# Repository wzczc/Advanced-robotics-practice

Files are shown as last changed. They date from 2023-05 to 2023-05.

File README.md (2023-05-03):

# Advanced-robotics-practice
code for "机器人高级实践"，**双轮足平衡小车**，实现细节见.docx文件  
小车整体图

* 小车硬件：**hardware** 文件夹
* 小车建模：**solidworks_models** 文件夹，小车轮腿图：
小车轮腿建模

* 开发平台：**STM32CubeMX** 和 **keil5** 联合开发
* 小车运行工程：**code-->MDK-ARM-->Encoder.uvprojx**
* 功能：
  * **平衡与抗干扰**

https://user-images.githubusercontent.com/94534877/235918275-014c7818-3400-4d11-a03c-7880798e8d1c.mp4

  * **轮腿伸缩**

https://user-images.githubusercontent.com/94534877/235918329-b2903bcf-4b72-4534-91ec-1fd617b79910.mp4

  * **直立行走**：可以使用手机蓝牙app(code文件夹里的base.apk.1)控制小车的前进、后退、左转、右转和停止

https://user-images.githubusercontent.com/94534877/235919043-f2ff14f8-f3b6-48d8-b337-52a1ab3aed3c.mp4

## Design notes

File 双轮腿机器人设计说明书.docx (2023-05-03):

1、 机器人总体介绍

1、设计原因

本款机器人名为双轮腿机器人，顾名思义，是以左右轮来代替传统的足式机器人的双脚，同时保留其腿式结构，使其既能像轮式机器人一样迅速，又能像足式机器人一样适应复杂的地形，从而满足我们对不同场景的各种各样的需求。

2、设计思路

本款机器人以腾讯近期发布的Ollie为基础，结合哔哩哔哩国炫学长的开源资料，自主设计机器人的机械结构与硬件选型；其中设计软件采用SolidWorks，采用3D打印的方式打印机器人的本体；硬件选择了四个舵机来控制机器人的四条大腿，大腿和小腿之间用轴承连接成旋转关节，小腿分别嵌在左右电机上，如此可以通过舵机来控制机器人的升降；电机采用带编码器的直流电机，信息实时传入主控板是stm32中，结合MPU6050测量的角度信息，从而控制车的基本平衡以及行走平衡。

3、基本功能

本款机器人目前实现的功能主要有：

1)能够实现基本的直立平衡状态；

2)给予人为干扰能保持平衡状态；

3)能够完成移动动作而保持不倒；

4)能够在移动时改变自己的移动方向；

5)能够在直立时完成腿部的升、降；

后续功能敬请期待！

4、优点
1)结构简单、双驱动，转角大且转弯半径小，甚至能实现原地回转，这使得两轮机器人运动十分灵活，线路轨迹多变，能够在空间狭窄的地区进行作业，克服了多轮机器人空间受限的缺点;

2)占地面积也小，由于机体一般采用分层设计，合理利用了空间，适用场所大大增加，作为短距离代步工具和娱乐机器人等都十分方便，也为机器人的小型化发展提供了参考方案;
3)低碳环保,所需驱动功率小，使用蓄电池供电就可满足电机运动需求，而且直驱电机噪音小、动力强劲，对节能有一定的积极作用;
4)能量损耗少，由于车轮数量只有两个，地面摩擦引起的损耗减少，并且两轮自平衡机器人没有刹车系统，不存在刹车片磨损等问题，制动仅靠控制器发出的电机运动指令，由电机转矩控制整个机器人运动或停止，这有利于提高物理能量利用率。

二、机器人本体介绍

机器人本体结构是机体结构和机械传动系统 (https://baike.baidu.com/item/%E6%9C%BA%E6%A2%B0%E4%BC%A0%E5%8A%A8%E7%B3%BB%E7%BB%9F/14743222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)，也是机器人的支承基础和执行机构。机器人本体基本结构由以下五部分组成：传动部件、机身及行走机构、臂部、腕部、手部。

本款机器人目前只包含机器人本体的两部分，即传动部件和机身及行走机构。 传动部件：主要是双轮腿机器人的四条腿与其相连接的部分构成多个旋转关节。舵机的旋转带动大腿的旋转；大腿通过轴承带动小腿的旋转；机器人腿部形状由张开到蜷缩在一起；高度下降，重心降低；舵机反方向旋转，机器人腿部打开，高度升高，重心升高。

机身及行走结构：机身框架由顶部的双层支撑板通过舵机与大腿相连，大腿连接小腿，小腿通过轴承连接电机，电机嵌在法兰上，外部连接车轮。其中支撑板用来固定主控板stm32、舵机、MPU6050、电机驱动模块、降压稳压模块和电源。行走结构即电机卡在法兰上连接车轮从而驱动电机使车轮转动，达到行走动作。

后续可以在双轮腿机器人的顶部支撑板安装机械臂，从而弥补其他三个结构的空缺，使机器人能够满足更多的需求。

三、硬件部分

硬件部分包括：24v电池一块，降压模块，驱动模块，MG996R舵机*4，有刷电机*2，核心板STM32F407,陀螺仪MPU6050*1.

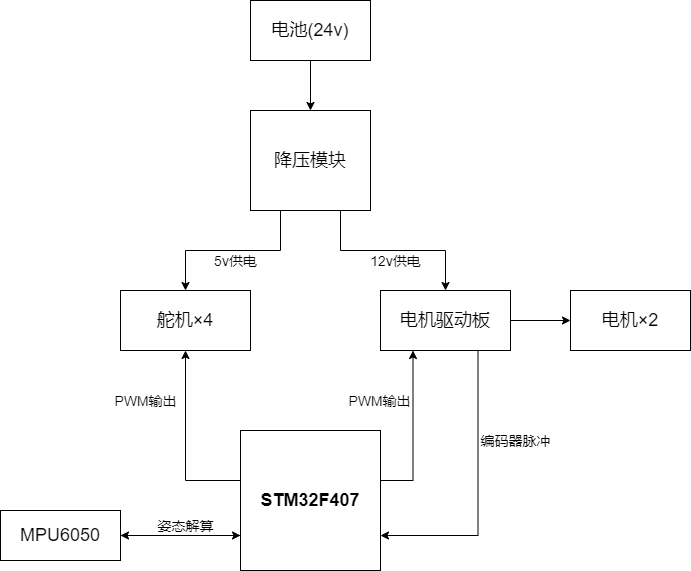
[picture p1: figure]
硬件框图

1.电池（24V）

2.降压型DC-DC电源模块XL4005

输入DC电压5-32V，输出DC电压0.8-30V，可实现双通道输出，输出电压比输入电压要低，只能通过模块内的精密电位器达到降压而不能升压。输出电流最大为5A，转换效率为92%。

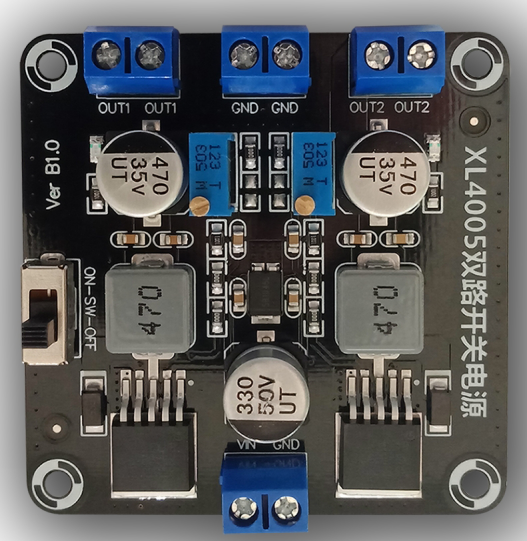
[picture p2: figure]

3.电机驱动模块AT8236

AT8236 芯片是一款单通道H桥电机驱动器，能够以高达6A的峰值电流双向控制单个电机。此模块内置两个AT8236，因此一个模块可以控制两个电机运转。芯片内部集成同步整流功能，能够有效降低系统功耗要求。利用电流衰减模式，可通过对输入信号进行脉宽调制(PWM) 来控制电机转速。此外，芯片对外还提供一个参考电压（Vref）输入引脚，用来设定驱动峰值电流的大小，此5V带稳压模块内的Vref引脚输入电压为5V。

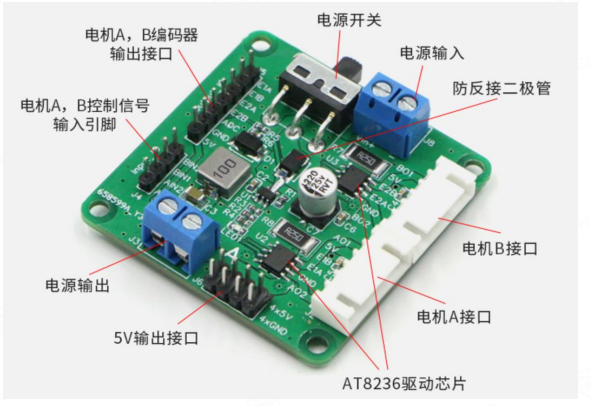
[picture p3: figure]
QQ截图20230224171222

4.MG996R舵机

和普通舵机一样，是一种位置伺服的驱动器，适用于那些需要角度不断变化并且可以保持的控制系统。其工作原理是：控制信号由接收机的通道进入信号调制芯片，获得直流偏置电压。它内部有一个基准电路，产生周期为20ms,宽度为1.5ms的基准信号，将获得的直流偏置电压和电位器的电压比较，获得电压输出。最后，电压差的正负输出到电机驱动芯片决定电机的正反转，当电机转速一定时，通过级联减速齿轮带动电位器旋转，使得电压差为0，电机停止转动。舵机的控制信号是PWM信号，利用占空比的变化改变舵机的位置。

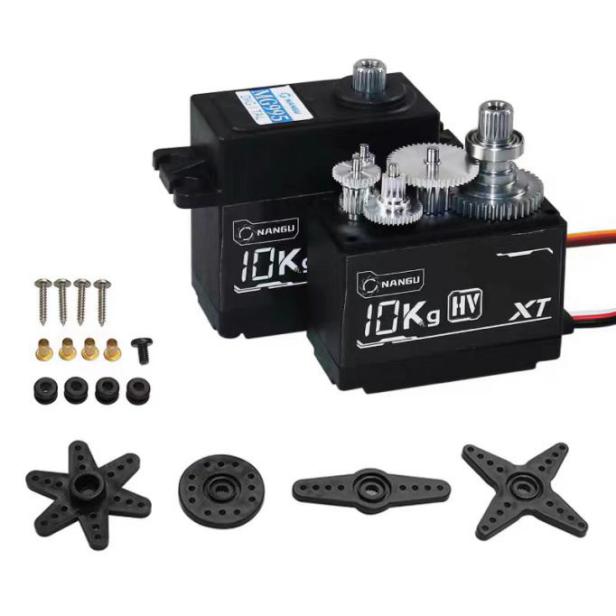
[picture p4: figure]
tb_image_share_1677231199930

5.带霍尔编码器的电机MG513P60

减速电机是在直流电机基础上，增加一个高精密的减速器的电机。一般直流电机的转速在一分钟几千上万转，增加减速器可以降低电机转速，增加电机扭矩，使得可控性更强。

选择减速电机的时候，电机的额定电压需要和我们选择的电池相匹配，常见的12V额定电压电机供电范围在11~16V之间，12V最佳。MG513P60_12V这款电机额定电压为12V，1：60的减速比，额定输出电流为0.36A，减速后空载转速为183rpm左右，扭矩达2kg*cm，最大负载能力高达6KG，再搭配65mm直径轮胎，速度大概0.5m/s，完全满足平衡小车的运动需求。另外这款电机还搭配了霍尔编码器，通过磁感应的原理，可以检测电机转速，从而实现速度检测和距离统计。

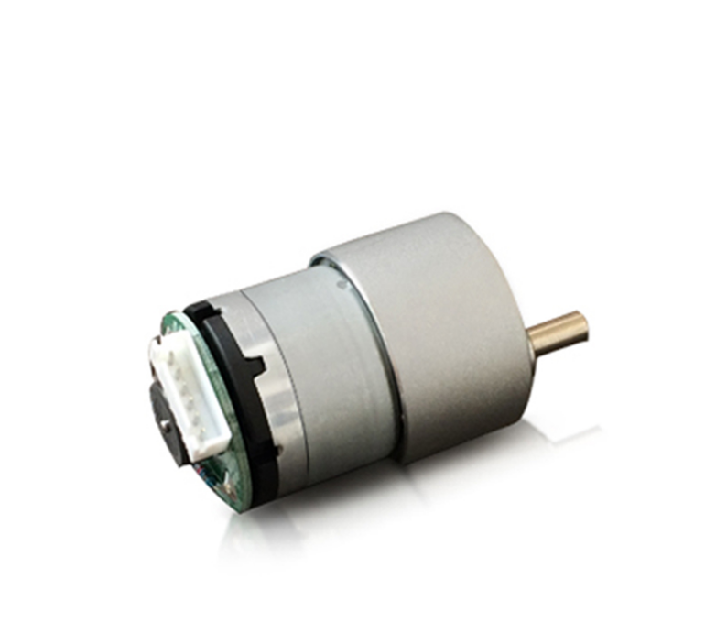
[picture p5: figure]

6.主控板STM32F407

STM32F407系列面向需要在小至10 x 10 mm的封装内实现高集成度、高性能、嵌入式存储器和外设的医疗、工业与消费类应用。
STM32F407/417提供了工作频率为168 MHz的Cortex™-M4内核（具有浮点单元）的性能。

性能：在168 MHz频率下，从Flash存储器执行时，STM32F407能够提供210 DMIPS/566 CoreMark性能，并且利用意法半导体的ART加速器实现了FLASH零等待状态。DSP指令和浮点单元扩大了产品的应用范围。

功效：该系列产品采用意法半导体90 nm工艺和ART加速器，具有动态功耗调整功能，能够在运行模式下和从Flash存储器执行时实现低至238 µA/MHz的电流消耗（@ 168 MHz）。

丰富的连接功能：出色的创新型外设：与STM32F4x5系列相比，STM32F407产品还具有符合IEEE 1588 v2标准要求的以太网MAC10和能够连接CMOS照相机传感器的8~14位并行照相机接口。

·2个USB OTG（其中一个支持HS）

·音频：专用音频PLL和2个全双工I²S

·通信接口多达15个（包括6个速度高达11.25 Mb/s的USART、3个速度高达45 Mb/s的SPI、3个I²C、2个CAN和1个SDIO）

·模拟：2个12位DAC、3个速度为2.4 MSPS或7.2 MSPS（交错模式）的12位ADC

·定时器多达17个：频率高达168 MHz的16和32位定时器

·可以利用支持Compact Flash、SRAM、PSRAM、NOR和NAND存储器的灵活静态存储器控制器轻松扩展存储容量

·基于模拟电子技术的真随机数发生器

STM32F407产品系列具有512KB~1MB Flash和192KB SRAM，采用尺寸小至10 x 10 mm的100~176引脚封装。

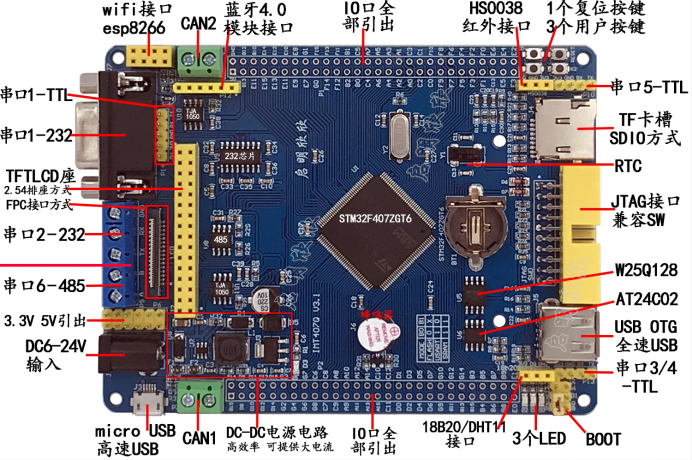
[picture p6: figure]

7.MPU6050

MPU-6050 是6轴运动处理传感器，它集成了 3 轴MEMS陀螺仪，3 轴MEMS加速度计，以及一个可扩展的数字运动处理器DMP。使用它就是为了得到待测物体（如四轴飞行器、平衡小车）x、y、z轴的倾角（俯仰角Pitch、翻滚角Roll、偏航角Yaw）。我们通过 I2C 读取到 MPU6050 的六个数据（三轴加速度 AD 值、三轴角速度 AD 值）经过姿态融合后就可以得到 Pitch、Roll、Yaw角。机器人搭载MPU-6050后测出实时三轴加速度和三轴角速度值，返回的数据反映小车姿态，相关程序处理后控制小车平衡。

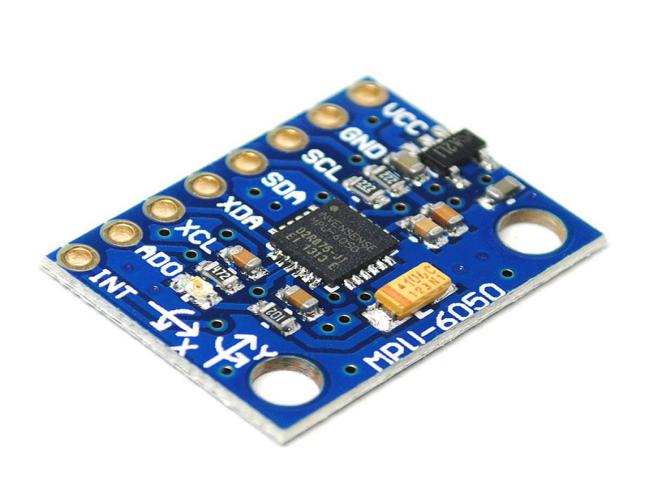
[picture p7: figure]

最后搭建出来的实物为：

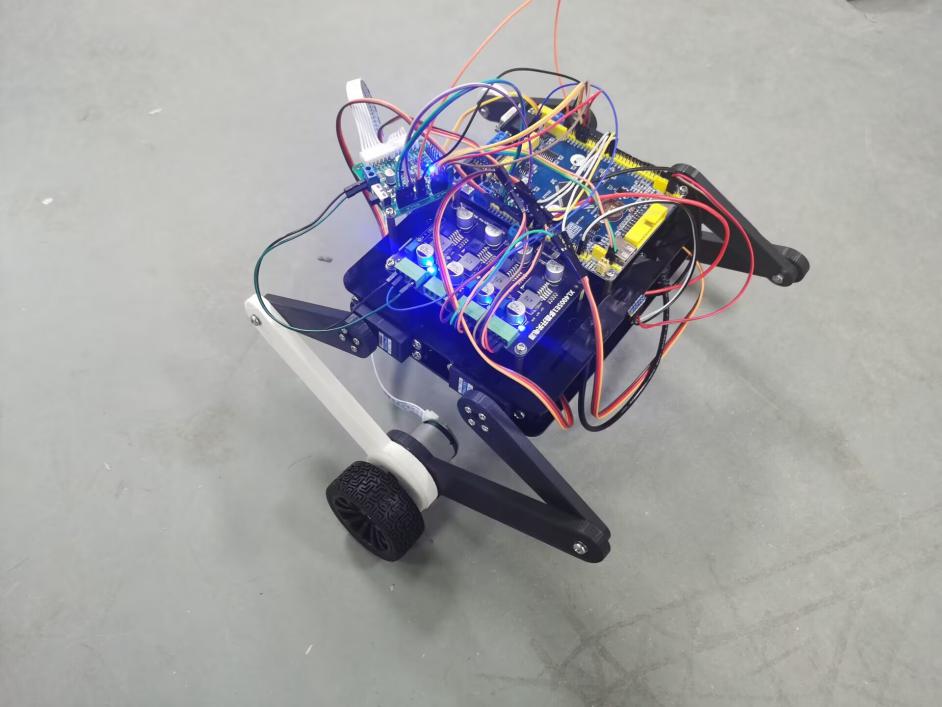
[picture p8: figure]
7E81C18BE3AB505F0FD8E452D66519CA

4、 软件

1.开发工具

使用keil 5和STM32CubeMX联合编写代码。keil5是一款单片机的软件开发系统，功能十分强大；

STM32CubeMX是STM32芯片的图形化操作界面，可以以图形界面的方式很方便地给所需功能进行配置，并且自动生成HAL库的配置代码，免去了自己查手册编写配置代码的繁琐步骤。

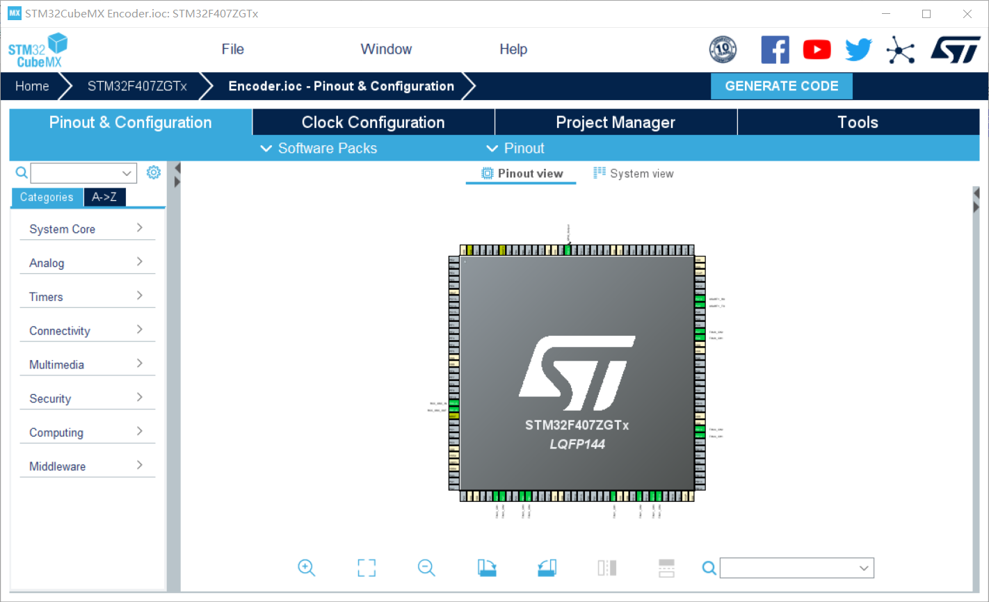
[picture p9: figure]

2.软件资源

GPIO：

1)PG13：作GPIO输出功能，用来点亮LED灯从而判断达到了某些状态。我们这里用它的闪烁来指示进入了定时器中断；

2)PF6、7、8、9：上拉输入模式，用来判断按键是否按下从而切换不同的模式。

TIM定时器：

1)TIM1：四个通道均作PWM生成功能，对应的引脚为PE9、PE11、PE13、PE14，使用如下函数：

控制TIM1不同的通道生成不同占空比的PWM波从而驱动电机。

2)TIM2：作计时功能。TIM2定时器的时钟频率是84MHz，我们设置预分频系数为840，自动重装载值为500：

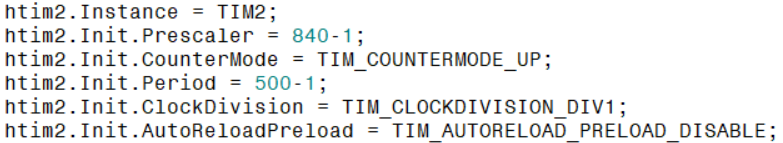
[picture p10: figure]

因此就可产生5ms的定时器中断，并在中断函数中编写控制算法控制小车的平衡。

3)TIM3：与TIM1一样，四个通道均作PWM生成功能，对应的引脚为PA6、PA7、PB0、PB1，产生不同占空比的PWM波控制舵机旋转的角度。

4)TIM4、8：使用它们的编码器模式功能，对应引脚为PD12、PD13、PC6、PC7，调用如下函数：

可获得左右两个轮子的编码器读数。

USART1：发送数据的功能，用到的引脚PA9、PA10。在这里，我们这里配合无线下载器传输平衡车的状态数据（车的速度和yaw、pitch、roll三个角度）发到电脑上的串口调试助手，以实时观察小车的状态。

DMP：MPU6050的加速库，用来加速MPU6050的数据处理。

蓝牙模块上位机：使用蓝牙app在手机上控制小车的前进、后退、左转、右转和停止：

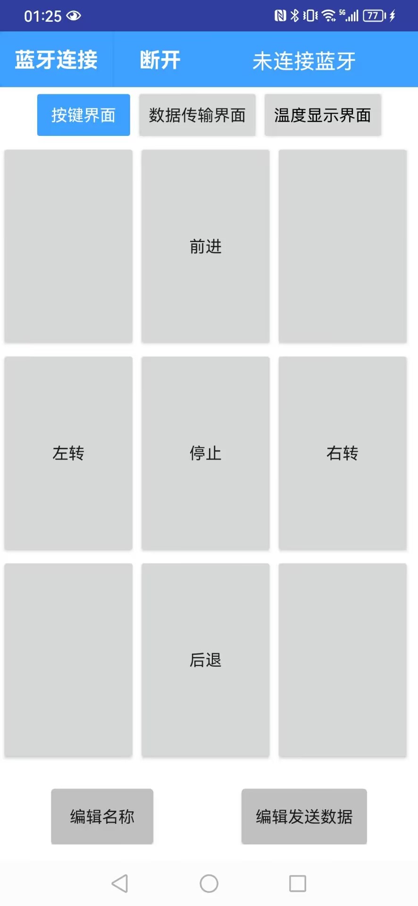
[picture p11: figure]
33618EE7FDCFAD0122F62B28D3B00625

相关的通信协议如下：

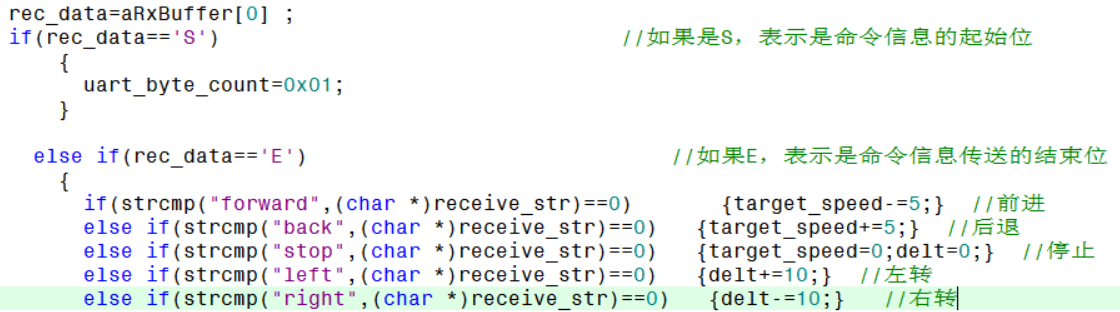
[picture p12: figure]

3.控制算法

使用的是两环并级PID算法，分别是PD调节的直立环（正反馈）和PI调节的速度环（负反馈），程序设计流程如下：

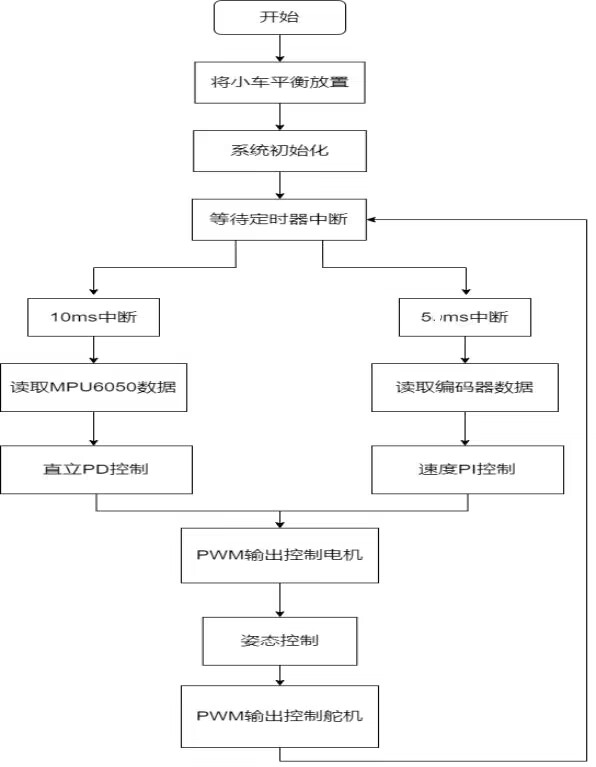
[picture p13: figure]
AC344A784FE81C7BA1DF45E036AFA032

五、操作流程

我们分别给小车设置了按键控制模式和蓝牙控制模式

1.按键控制模式

使用单片机上的四个按键来对应四个不同的模式：

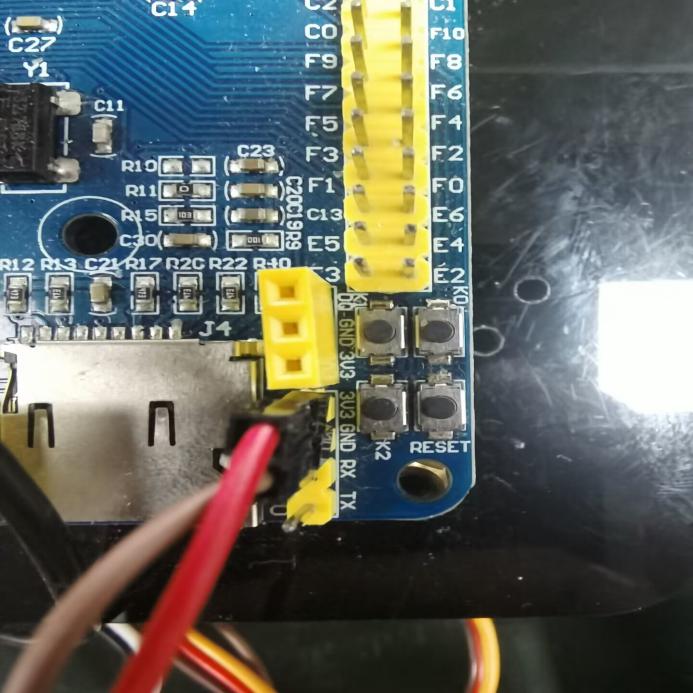
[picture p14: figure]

KEY0（右下按键）：为启动小车和平衡模式的按键。首先将小车放在大致的平衡位置，按下KEY0，小车可以在舵机转角为10°的情况下保持稳定平衡，之后轻拍小车，小车会有短暂的摇晃但马上可以恢复平衡状态。此模式展示的是小车平衡状态以及其抗干扰的性能。

KEY1（右上按键）：为平衡状态下伸缩腿模式的按键。首先将小车放在大致的平衡位置，按下KEY1，小车在短暂平衡后舵机转角会从10°连续改变至35°，在35°下短暂平衡后，舵机转角又会恢复至10°，如此反复。此模式展示的是小车在腿上下伸缩的情况下仍能保持平衡的性能。

KEY2（左上按键）：为小车行驶模式的按键。首先将小车放在大致的平衡位置，按下KEY2，在短暂平衡后，小车会开始逐渐向前加速至设定值，行驶一段时间后停止并平衡，之后在向后行驶一段时间再平衡。此模式展示的是小车可以稳定平衡行驶的性能。

KEY3（左下按键）：为小车行驶状态下伸缩腿模式的按键。首先将小车放在大致的平衡位置，按下KEY3，在短暂平衡后，小车会开始向前行驶，并在行驶过程中将腿抬起至25°随后再降至10°，如此反复。此模式展示的是小车在行驶时腿可以反复上下屈伸的性能。

2. 蓝牙控制模式

首先将小车放置在大致平衡位置，启动小车；然后打开蓝牙app与小车上的蓝牙模块HC-05配对；之后在app里设置发送给小车的数据以控制小车不同的运动，我们这里设置了如下5个运动方式：

按下相应的键，小车就会有不同的运动，并且按键次数的不同也会有不同的速度，如按一次“前进”是缓慢前进，连续按两三次“前进”则是快速前进，其他按键的运动模式亦是如此。

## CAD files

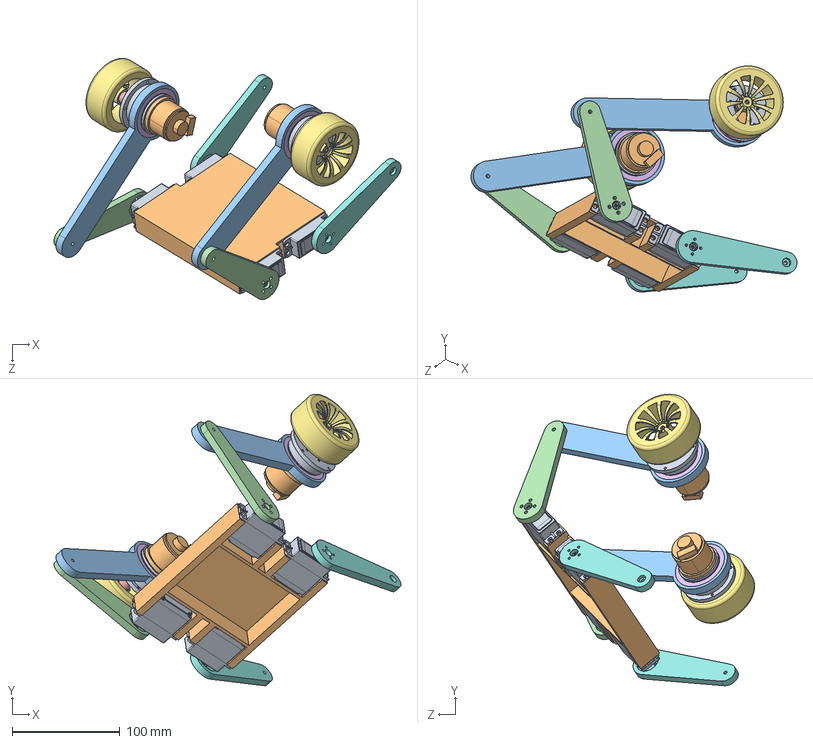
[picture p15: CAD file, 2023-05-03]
solidworks_models/轮腿.SLDASM
322.0 x 270.5 x 223.7 mm
打印件 x 2
马达三维模型 x 2
small leg2 x 2
大腿 x 2
轴直径6mm_车轮65mm联轴器.stp x 2
零件4 x 2
智能车轮_直径65mm.stp x 2
大腿 2 x 2
标准舵机外形3D.step x 4
车头

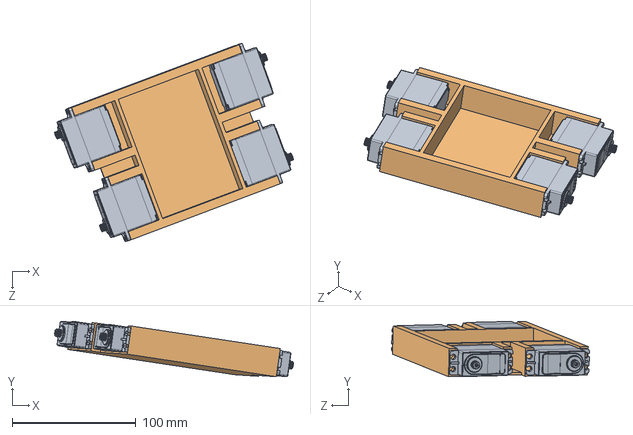
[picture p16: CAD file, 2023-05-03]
solidworks_models/盒.SLDASM
193.3 x 44.8 x 160.1 mm
标准舵机外形3D.step x 4
车头

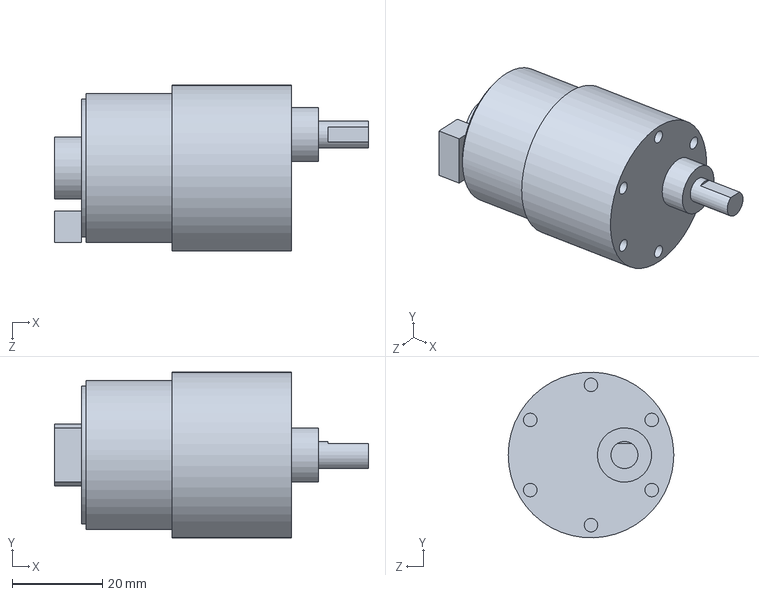
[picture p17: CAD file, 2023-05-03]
solidworks_models/马达.SLDPRT
69.4 x 36.6 x 36.6 mm

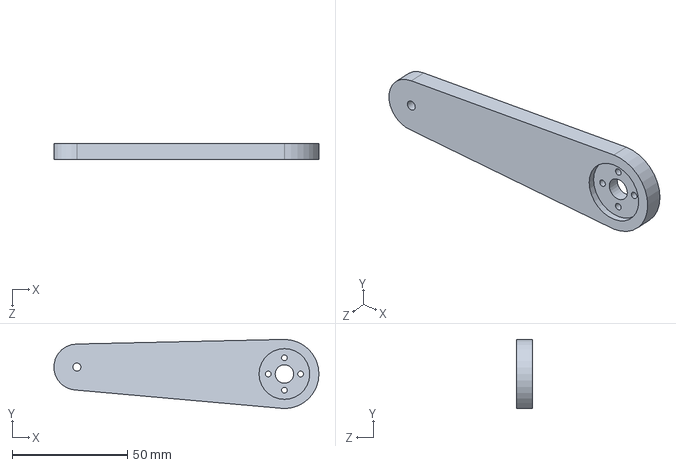
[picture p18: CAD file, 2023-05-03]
solidworks_models/大腿 2.SLDPRT
114.9 x 30.0 x 7.00 mm

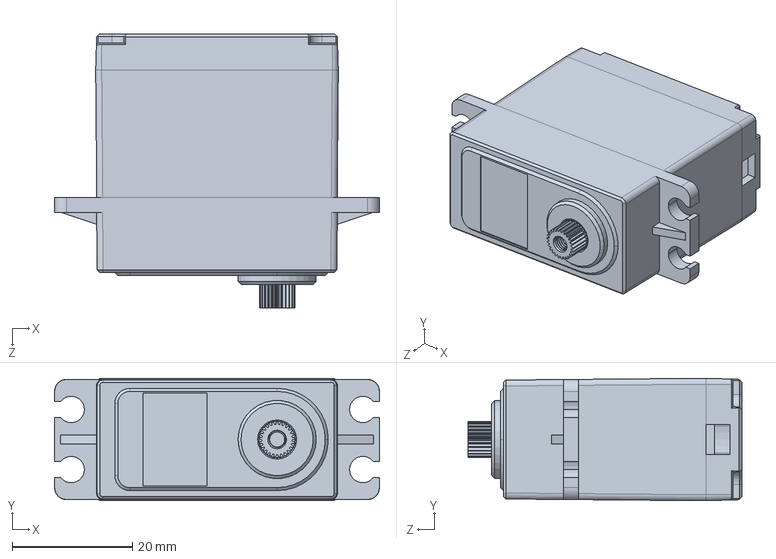
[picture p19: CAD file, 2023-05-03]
solidworks_models/标准舵机外形3D.step.SLDPRT
54.1 x 20.4 x 45.7 mm

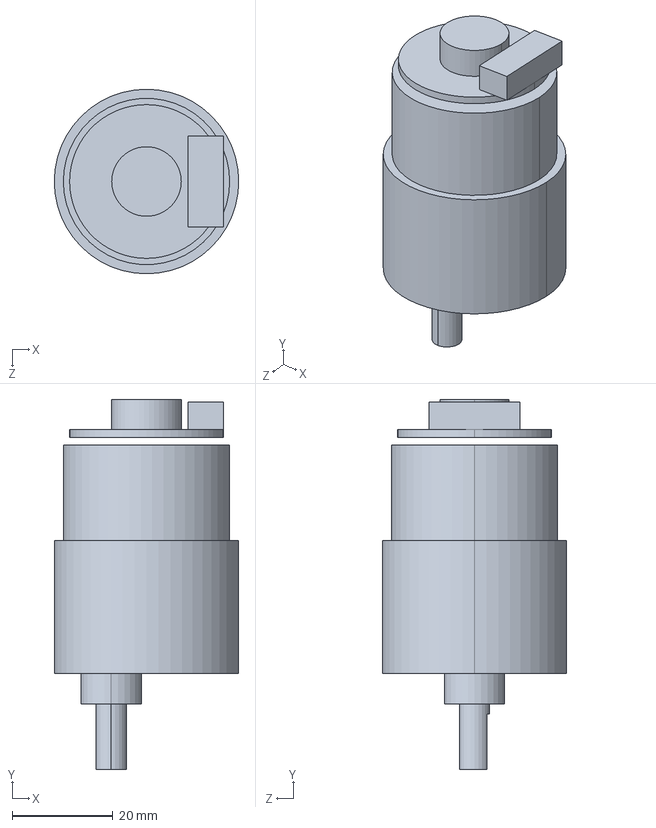
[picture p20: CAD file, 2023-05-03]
solidworks_models/马达三维模型.SLDPRT
36.6 x 73.4 x 36.6 mm

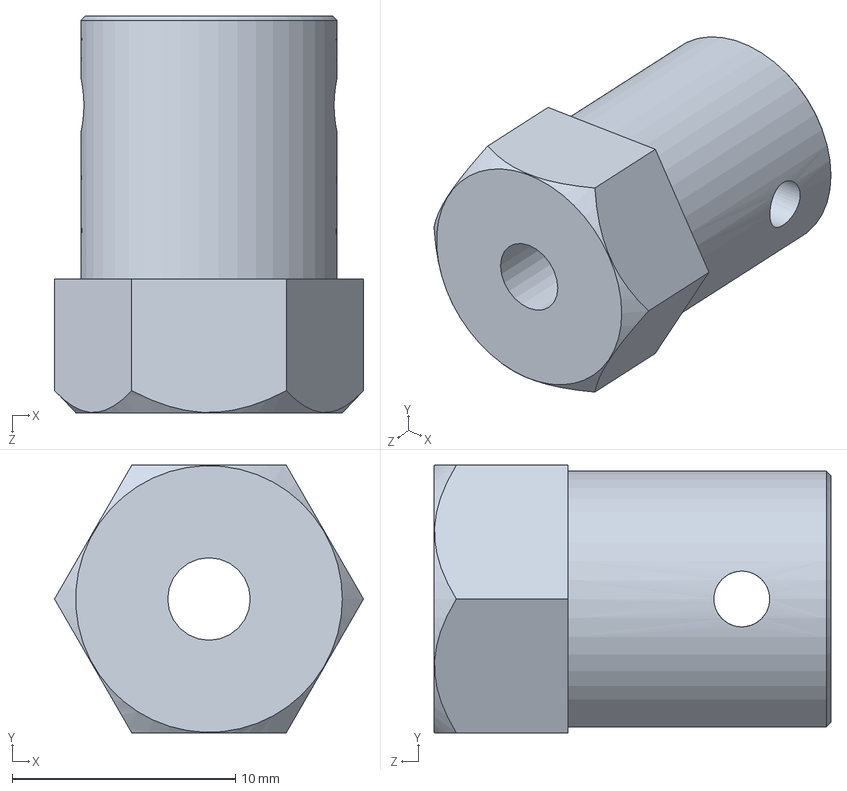
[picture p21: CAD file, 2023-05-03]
solidworks_models/轴直径6mm_车轮65mm联轴器.stp.SLDPRT
13.9 x 12.0 x 17.8 mm

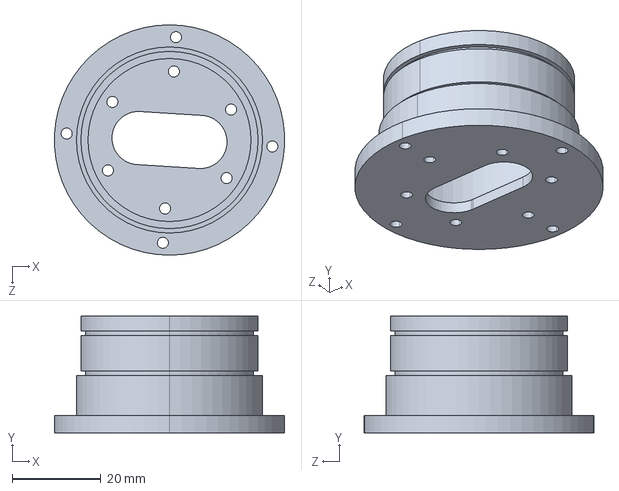
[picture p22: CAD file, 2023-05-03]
solidworks_models/打印件_默认_sldprt.STEP
51.9 x 26.4 x 52.0 mm

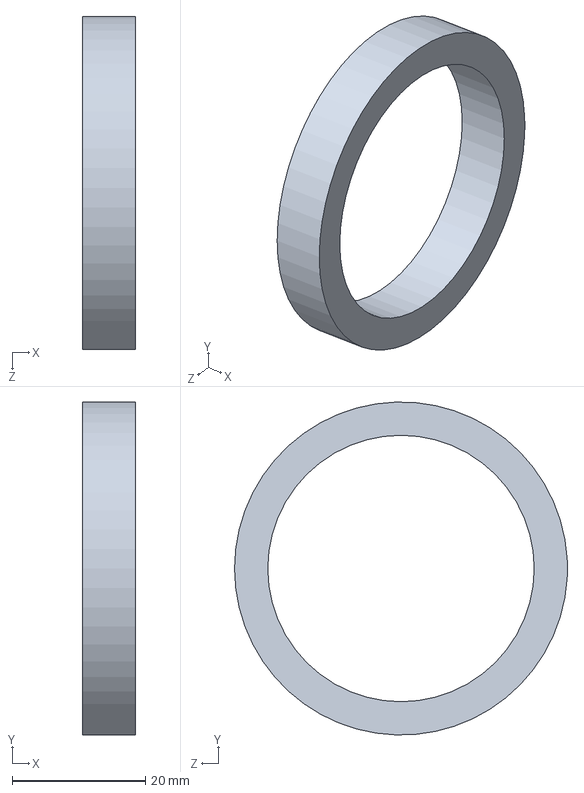
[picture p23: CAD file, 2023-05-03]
solidworks_models/零件4.SLDPRT
8.00 x 50.0 x 50.0 mm

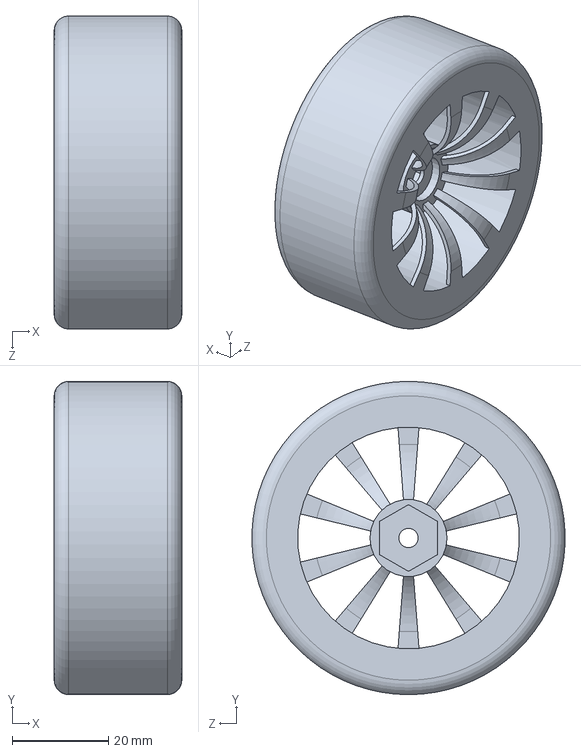
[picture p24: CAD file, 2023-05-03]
solidworks_models/智能车轮_直径65mm.stp.SLDPRT
26.5 x 65.0 x 64.9 mm

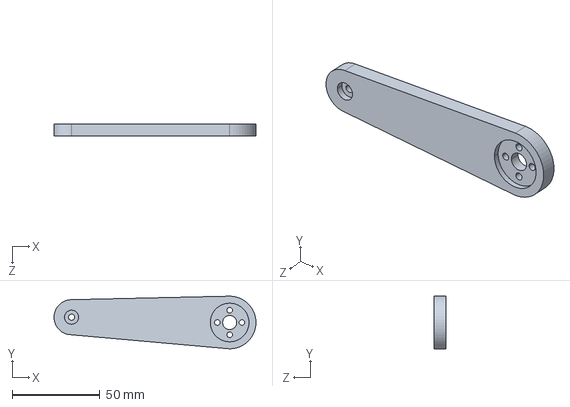
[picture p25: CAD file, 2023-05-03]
solidworks_models/大腿_默认_sldprt.STEP
115.0 x 30.0 x 7.00 mm

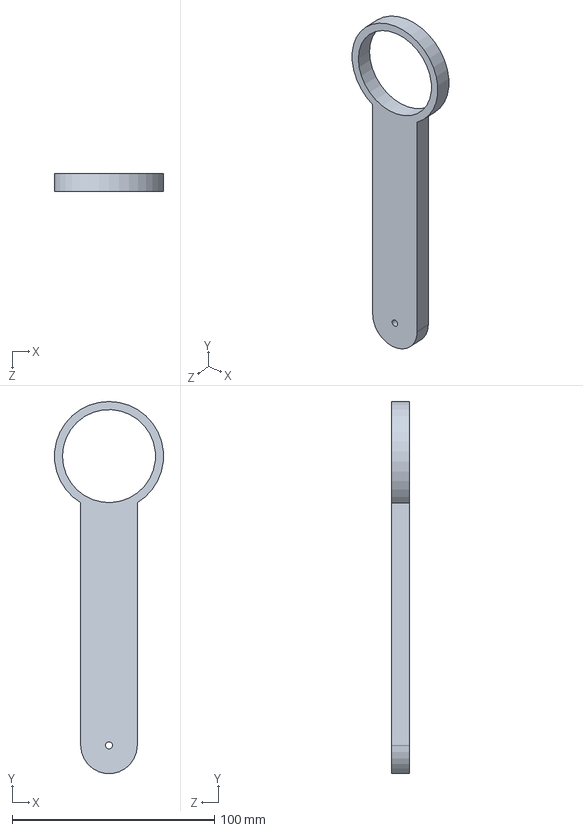
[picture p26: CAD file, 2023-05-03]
solidworks_models/small leg2.SLDPRT
53.8 x 184.0 x 9.00 mm

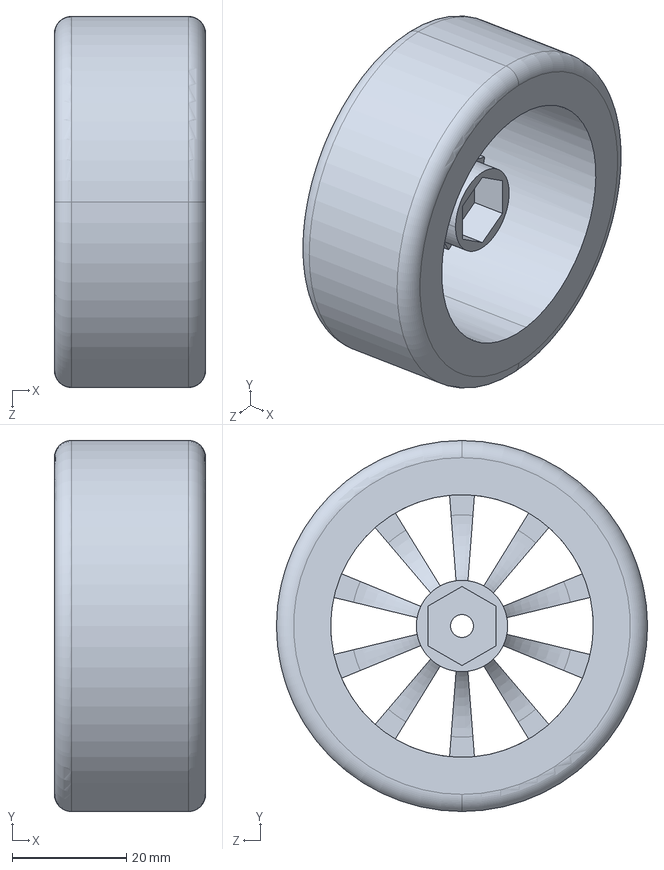
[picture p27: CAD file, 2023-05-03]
solidworks_models/智能车轮_直径65mm.stp_默认_sldprt.STEP
26.5 x 65.0 x 65.0 mm

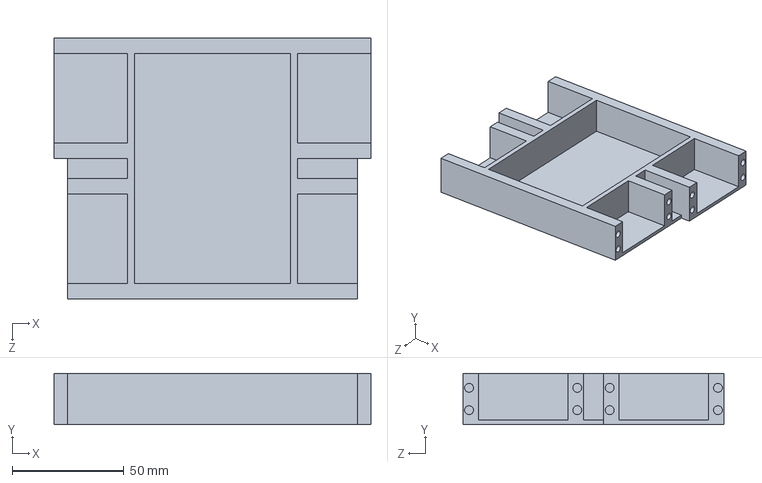
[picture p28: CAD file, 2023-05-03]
solidworks_models/车头_默认_sldprt.STEP
142.0 x 23.0 x 117.0 mm

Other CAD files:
solidworks_models/零件4_默认_sldprt.STEP
solidworks_models/大腿.SLDPRT
solidworks_models/右2大腿.SLDPRT
solidworks_models/small leg1_默认_sldprt.STEP
solidworks_models/small leg1.SLDPRT
solidworks_models/small leg2_默认_sldprt.STEP
solidworks_models/大腿 2.STL
solidworks_models/大腿 2_默认_sldprt.STEP
solidworks_models/大腿.STL
solidworks_models/左2大腿.SLDPRT
solidworks_models/打印件.SLDPRT
solidworks_models/打印件.STL
solidworks_models/标准舵机外形3D.step_默认_sldprt.STEP
solidworks_models/轴承.SLDPRT
solidworks_models/轴直径6mm_车轮65mm联轴器.stp_默认_sldprt.STEP
solidworks_models/马达三维模型_默认_sldprt.STEP

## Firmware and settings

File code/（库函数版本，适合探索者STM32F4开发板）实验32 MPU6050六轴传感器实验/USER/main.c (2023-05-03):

#include "sys.h"
#include "delay.h"
#include "usart.h"
#include "led.h"
#include "key.h"
#include "lcd.h"
#include "mpu6050.h"
#include "inv_mpu.h"
#include "inv_mpu_dmp_motion_driver.h" 

//ALIENTEK 探索者STM32F407开发板 实验32
//MPU6050六轴传感器 实验 -库函数版本
//技术支持：www.openedv.com
//淘宝店铺：http://eboard.taobao.com  
//广州市星翼电子科技有限公司  
//作者：正点原子 @ALIENTEK

//串口1发送1个字符 
//c:要发送的字符
//void usart1_send_char(u8 c)
//{

//	while(USART_GetFlagStatus(USART1,USART_FLAG_TC)==RESET); 
//    USART_SendData(USART1,c);   

//} 
////传送数据给匿名四轴上位机软件(V2.6版本)
////fun:功能字. 0XA0~0XAF
////data:数据缓存区,最多28字节!!
////len:data区有效数据个数
//void usart1_niming_report(u8 fun,u8*data,u8 len)
//{
//	u8 send_buf[32];
//	u8 i;
//	if(len>28)return;	//最多28字节数据 
//	send_buf[len+3]=0;	//校验数置零
//	send_buf[0]=0X88;	//帧头
//	send_buf[1]=fun;	//功能字
//	send_buf[2]=len;	//数据长度
//	for(i=0;i<len;i++)send_buf[3+i]=data[i];			//复制数据
//	for(i=0;i<len+3;i++)send_buf[len+3]+=send_buf[i];	//计算校验和	
//	for(i=0;i<len+4;i++)usart1_send_char(send_buf[i]);	//发送数据到串口1 
//}
////发送加速度传感器数据和陀螺仪数据
////aacx,aacy,aacz:x,y,z三个方向上面的加速度值
////gyrox,gyroy,gyroz:x,y,z三个方向上面的陀螺仪值
//void mpu6050_send_data(short aacx,short aacy,short aacz,short gyrox,short gyroy,short gyroz)
//{
//	u8 tbuf[12]; 
//	tbuf[0]=(aacx>>8)&0XFF;
//	tbuf[1]=aacx&0XFF;
//	tbuf[2]=(aacy>>8)&0XFF;
//	tbuf[3]=aacy&0XFF;
//	tbuf[4]=(aacz>>8)&0XFF;
//	tbuf[5]=aacz&0XFF; 
//	tbuf[6]=(gyrox>>8)&0XFF;
//	tbuf[7]=gyrox&0XFF;
//	tbuf[8]=(gyroy>>8)&0XFF;
//	tbuf[9]=gyroy&0XFF;
//	tbuf[10]=(gyroz>>8)&0XFF;
//	tbuf[11]=gyroz&0XFF;
//	usart1_niming_report(0XA1,tbuf,12);//自定义帧,0XA1
//}	
////通过串口1上报结算后的姿态数据给电脑
////aacx,aacy,aacz:x,y,z三个方向上面的加速度值
////gyrox,gyroy,gyroz:x,y,z三个方向上面的陀螺仪值
////roll:横滚角.单位0.01度。 -18000 -> 18000 对应 -180.00  ->  180.00度
////pitch:俯仰角.单位 0.01度。-9000 - 9000 对应 -90.00 -> 90.00 度
////yaw:航向角.单位为0.1度 0 -> 3600  对应 0 -> 360.0度
//void usart1_report_imu(short aacx,short aacy,short aacz,short gyrox,short gyroy,short gyroz,short roll,short pitch,short yaw)
//{
//	u8 tbuf[28]; 
//	u8 i;
//	for(i=0;i<28;i++)tbuf[i]=0;//清0
//	tbuf[0]=(aacx>>8)&0XFF;
//	tbuf[1]=aacx&0XFF;
//	tbuf[2]=(aacy>>8)&0XFF;
//	tbuf[3]=aacy&0XFF;
//	tbuf[4]=(aacz>>8)&0XFF;
//	tbuf[5]=aacz&0XFF; 
//	tbuf[6]=(gyrox>>8)&0XFF;
//	tbuf[7]=gyrox&0XFF;
//	tbuf[8]=(gyroy>>8)&0XFF;
//	tbuf[9]=gyroy&0XFF;
//	tbuf[10]=(gyroz>>8)&0XFF;
//	tbuf[11]=gyroz&0XFF;	
//	tbuf[18]=(roll>>8)&0XFF;
//	tbuf[19]=roll&0XFF;
//	tbuf[20]=(pitch>>8)&0XFF;
//	tbuf[21]=pitch&0XFF;
//	tbuf[22]=(yaw>>8)&0XFF;
//	tbuf[23]=yaw&0XFF;
//	usart1_niming_report(0XAF,tbuf,28);//飞控显示帧,0XAF
//} 
  
int main(void)
{ 
	u8 t=0,report=1;			//默认开启上报
	u8 key;
	float pitch,roll,yaw; 		//欧拉角
	short aacx,aacy,aacz;		//加速度传感器原始数据
	short gyrox,gyroy,gyroz;	//陀螺仪原始数据
	short temp;					//温度
	NVIC_PriorityGroupConfig(NVIC_PriorityGroup_2);//设置系统中断优先级分组2
	delay_init(168);  //初始化延时函数
	uart_init(115200);		//初始化串口波特率为500000
	LED_Init();					//初始化LED 
	KEY_Init();					//初始化按键
 	LCD_Init();					//LCD初始化
	MPU_Init();					//初始化MPU6050

//	while(mpu_dmp_init())
//	{
//		delay_ms(200);
// 		delay_ms(200);
//	}
	printf("%d\r\n",mpu_dmp_init());
	 		delay_ms(2000);

 	while(1)
	{
		if(mpu_dmp_get_data(&pitch,&roll,&yaw)==0)
		{
			temp=MPU_Get_Temperature();	//得到温度值
			MPU_Get_Accelerometer(&aacx,&aacy,&aacz);	//得到加速度传感器数据
			MPU_Get_Gyroscope(&gyrox,&gyroy,&gyroz);	//得到陀螺仪数据
			if(1)//GetData=0时 用于USMART调试MPU6050寄存器
			{
				
				if((t%10)==0)
				{ 		
					//temp值
					if(temp<0)
					{
						temp=-temp;		//转为正数
						//printf(" Temp:  -%d.%dC\r\n",temp/100,temp%10);
					}else
						//printf(" Temp:  %d.%dC\r\n",temp/100,temp%10);
						
					//pitch值
					temp=pitch*10;			
					if(temp<0)
					{
						temp=-temp;		//转为正数
						printf(" Pitch: -%d.%dC\r\n",temp/10,temp%10);
					}else
						printf(" Pitch:  %d.%dC\r\n",temp/10,temp%10);
					
					//roll值
					temp=roll*10;		
					if(temp<0)
					{
						temp=-temp;		//转为正数
						printf(" Roll:  -%d.%dC\r\n",temp/10,temp%10);
					}else
						printf(" Roll:  %d.%dC\r\n",temp/10,temp%10);
					
					//yaw值
					temp=yaw*10;
					if(temp<0)
					{
						temp=-temp;		//转为正数
						printf(" Yaw:  -%d.%dC\r\n",temp/10,temp%10);
					}else
						printf(" Yaw:   %d.%dC\r\n",temp/10,temp%10);
				
					printf("\r\n");
					t=0;
					LED0=!LED0;//LED闪烁
				}

			}
			
    }
		t++; 
//		//while(mpu_dmp_get_data(&pitch,&roll,&yaw)!=0){delay_ms(1);}
//			temp=MPU_Get_Temperature();	//得到温度值
//			MPU_Get_Accelerometer(&aacx,&aacy,&aacz);	//得到加速度传感器数据
//			MPU_Get_Gyroscope(&gyrox,&gyroy,&gyroz);	//得到陀螺仪数据
//			mpu6050_send_data(aacx,aacy,aacz,gyrox,gyroy,gyroz);//用自定义帧发送加速度和陀螺仪原始数据
//			usart1_report_imu(aacx,aacy,aacz,gyrox,gyroy,gyroz,(int)(roll*100),(int)(pitch*100),(int)(yaw*10));
//			printf("ax=%hd,ay=%hd,az=%hd,gx=%hd,gy=%hd,gz=%hd,roll=%d,pitch=%d,yaw=%d \r\n",
//							aacx,aacy,aacz,gyrox,gyroy,gyroz,(int)(roll*100),(int)(pitch*100),(int)(yaw*10));
//		delay_ms(200);
//			if(report)mpu6050_send_data(aacx,aacy,aacz,gyrox,gyroy,gyroz);//用自定义帧发送加速度和陀螺仪原始数据
//			if(report)usart1_report_imu(aacx,aacy,aacz,gyrox,gyroy,gyroz,(int)(roll*100),(int)(pitch*100),(int)(yaw*10));
//			mpu6050_send_data(aacx,aacy,aacz,gyrox,gyroy,gyroz);//用自定义帧发送加速度和陀螺仪原始数据
//			usart1_report_imu(aacx,aacy,aacz,gyrox,gyroy,gyroz,(int)(roll*100),(int)(pitch*100),(int)(yaw*10));
//		
//		key=KEY_Scan(0);
//		if(key==KEY0_PRES)
//		{
//			report=!report;
//			if(report)LCD_ShowString(30,170,200,16,16,"UPLOAD ON ");
//			else LCD_ShowString(30,170,200,16,16,"UPLOAD OFF");
//		}
//		if(mpu_dmp_get_data(&pitch,&roll,&yaw)==0)
//		{ 
//			temp=MPU_Get_Temperature();	//得到温度值
//			MPU_Get_Accelerometer(&aacx,&aacy,&aacz);	//得到加速度传感器数据
//			MPU_Get_Gyroscope(&gyrox,&gyroy,&gyroz);	//得到陀螺仪数据
////			if(report)mpu6050_send_data(aacx,aacy,aacz,gyrox,gyroy,gyroz);//用自定义帧发送加速度和陀螺仪原始数据
////			if(report)usart1_report_imu(aacx,aacy,aacz,gyrox,gyroy,gyroz,(int)(roll*100),(int)(pitch*100),(int)(yaw*10));
//			mpu6050_send_data(aacx,aacy,aacz,gyrox,gyroy,gyroz);//用自定义帧发送加速度和陀螺仪原始数据
//			usart1_report_imu(aacx,aacy,aacz,gyrox,gyroy,gyroz,(int)(roll*100),(int)(pitch*100),(int)(yaw*10));
//			
//			if((t%10)==0)
//			{ 
//				if(temp<0)
//				{
//					LCD_ShowChar(30+48,200,'-',16,0);		//显示负号
//					temp=-temp;		//转为正数
//				}else LCD_ShowChar(30+48,200,' ',16,0);		//去掉负号 
//				LCD_ShowNum(30+48+8,200,temp/100,3,16);		//显示整数部分	    
//				LCD_ShowNum(30+48+40,200,temp%10,1,16);		//显示小数部分 
//				temp=pitch*10;
//				if(temp<0)
//				{
//					LCD_ShowChar(30+48,220,'-',16,0);		//显示负号
//					temp=-temp;		//转为正数
//				}else LCD_ShowChar(30+48,220,' ',16,0);		//去掉负号 
//				LCD_ShowNum(30+48+8,220,temp/10,3,16);		//显示整数部分	    
//				LCD_ShowNum(30+48+40,220,temp%10,1,16);		//显示小数部分 
//				temp=roll*10;
//				if(temp<0)
//				{
//					LCD_ShowChar(30+48,240,'-',16,0);		//显示负号
//					temp=-temp;		//转为正数
//				}else LCD_ShowChar(30+48,240,' ',16,0);		//去掉负号 
//				LCD_ShowNum(30+48+8,240,temp/10,3,16);		//显示整数部分	    
//				LCD_ShowNum(30+48+40,240,temp%10,1,16);		//显示小数部分 
//				temp=yaw*10;
//				if(temp<0)
//				{
//					LCD_ShowChar(30+48,260,'-',16,0);		//显示负号
//					temp=-temp;		//转为正数
//				}else LCD_ShowChar(30+48,260,' ',16,0);		//去掉负号 
//				LCD_ShowNum(30+48+8,260,temp/10,3,16);		//显示整数部分	    
//				LCD_ShowNum(30+48+40,260,temp%10,1,16);		//显示小数部分  
//				t=0;
//				LED0=!LED0;//LED闪烁
//			}
//		}
//		t++; 
	} 	
}

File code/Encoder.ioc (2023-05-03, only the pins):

Mcu.UserName=STM32F407ZGTx
PA10.Signal=USART1_RX
PA6.Signal=S_TIM3_CH1
PA7.Signal=S_TIM3_CH2
PA9.Signal=USART1_TX
PB0.Signal=S_TIM3_CH3
PB1.Signal=S_TIM3_CH4
PC6.Signal=S_TIM8_CH1
PC7.Signal=S_TIM8_CH2
PD12.Signal=S_TIM4_CH1
PD13.Signal=S_TIM4_CH2
PE11.Signal=S_TIM1_CH2
PE13.Signal=S_TIM1_CH3
PE14.Signal=S_TIM1_CH4
PE9.Signal=S_TIM1_CH1
PG13.Signal=GPIO_Output
PH0-OSC_IN.Signal=RCC_OSC_IN
PH1-OSC_OUT.Signal=RCC_OSC_OUT
